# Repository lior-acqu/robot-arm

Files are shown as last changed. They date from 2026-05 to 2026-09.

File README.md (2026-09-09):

Welcome to Dedekind's GitHub repo. Here you can find:
- All the 3D files I used to print the robot.
- Three example C++ scripts to control the Arduino. More info on them below.
	- Rock-paper-scissors
	- Pick-and-place (called inversekinematics)
	- Manual servo control (servos)
# Scripts
## Rock-Paper-Scissors
When you run this script, you can play rock-paper-scissors with your robot arm. Opening the gripper means paper, closing it means rock, a quick open-close motion means scissors. Have fun!
## Pick-And-Place (inversekinematics)
In this script, you can make the robot pick up things like pens and erasers. If you use the same servos as I do, the weight of these objects is no problem.
The file contains many comments. If you need to change something in the script, you can find everything with ease. Possible things you may want to change:
- Positions: In the `loop()` function, you can change the numbers in the `inverseKin()` calls. The first number is the distance in cm from the shoulder joint. The second one is the angle of the base motor in degrees.
- Corrections: In case you have not been very precise in the assembly of the robot, and now, e.g. the shoulder joint is off by 10 degrees, you can enter corrections in the script that get taken into account by the inverse kinematics function. Just change `shoulder_corr` to `10`.
## Manual Servo Control (servos)
Here, you first run the Arduino script in the IDE. The robot will go to its home position.
Then, you open the `control.py` script. Here, you will probably need to change the `SERIAL_PORT` variable. You can find the right name for the port in the Arduino IDE in the top-left dropdown menu where you can select your Arduino board. Once the name is correct, you can run the script and then control all 5 servos with your keyboard.
- The base uses Q & A.
- The shoulder uses W & S.
- The elbow uses E & D.
- The wrist uses R & F.
- The gripper uses T & G.
# Known Issues
The robot arm works well. The points below are just small improvements.
1. Sometimes, the gripping motion does not work well. When it grabs a thin pen, the two gear racks sometimes lose contact with their rails and the gripper gear. The pen then drops on the ground and the two gear racks are now a bit wider apart.
	- Possible fix: The clamps should not be at the very end of the gear rack. Instead, they should have a safe margin of 1-2cm to make sure the gear rack is still fully supported by the guardrails.
2. Some parts are not designed in a way that they could be screwed in very tightly. They tend to be a bit loose.
	- Possible fix: Change the parts so that they are a bit easier to assemble, make things a bit tighter where you can.
# Materials
## 3D Parts
The uploaded parts work well. I usually added -0.07mm of X-Y-contour-compensation to make sure that the parts fit.
Support is not needed, except for `ForearmBase.stl` and `UpperArmBase.stl`.
My personal recommendation: Take my files only as an inspiration and design your own parts!
### Used Filament
I used eSUN's PLA+. I think that any regular filament (PLA, PETG) works just fine.
## Used Electronics
### Servos
- 2x MG996R (by Miuzei)
- 2x MG90S (by Miuzei)
- 1x SG90
### Other Electronics
- 10A 5V power supply (by Leicke, yes, it needs that much current)
- Arduino UNO
- PWM Servo Driver PCA9685
## Screws
- All screws are M3 (6mm & 10mm length) with matching nuts.
# Assembly
The assembly is quite intuitive, because there is always only one part that fits into the other part. Only a few remarks are necessary.
- The only place where you need 6mm M3 screws is when connecting the wrist motor to the gripper. In all other cases, 10mm is usually easier.
- The electronic parts do not need to be screwed into the base. The inner walls are designed to ensure perfect fit for all parts.
- In the base, there are some parts that are separated from the main part. Feel free to add weights into these parts. You can cover them with the printed weight caps.
- Each motor needs an attachment piece. In the middle of this attachment piece, just use the screw that was delivered in the same package as the motor. The MG996R motors have a separate attachment piece (`MG996RAttachment.stl`). The other ones use `NormalMotorAttachment.stl`.
- If the cables are too short for some motors, just use extension cables. I also did that.
- The base and the gripper both have small pockets where you can insert the nuts to make it easier to screw everything together.
- Be careful that all cables are plugged in correctly. 
If you have some more questions, just send me a message on LinkedIn (https://www.linkedin.com/in/liorporath/).

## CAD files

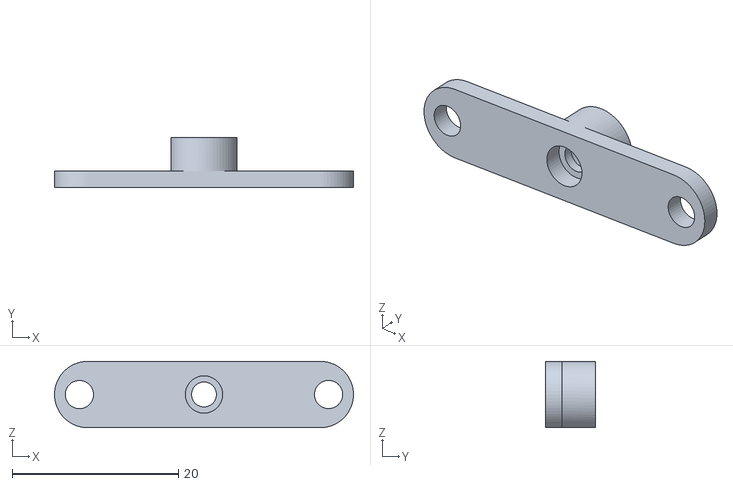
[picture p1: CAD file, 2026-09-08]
NormalMotorAttachment.stl
36.0 x 6.00 x 8.00

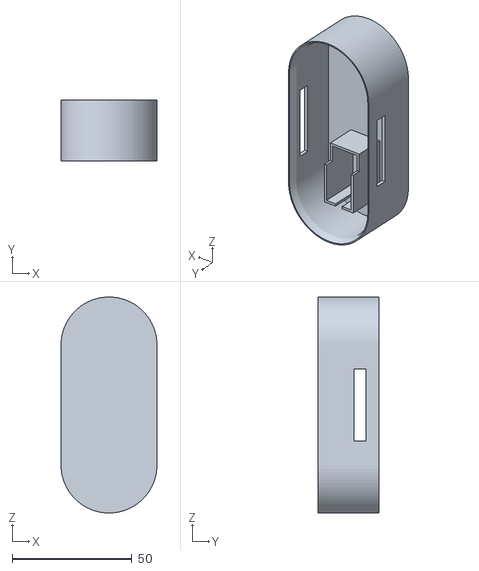
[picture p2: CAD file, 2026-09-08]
ForearmBase.stl
40.0 x 25.3 x 90.0

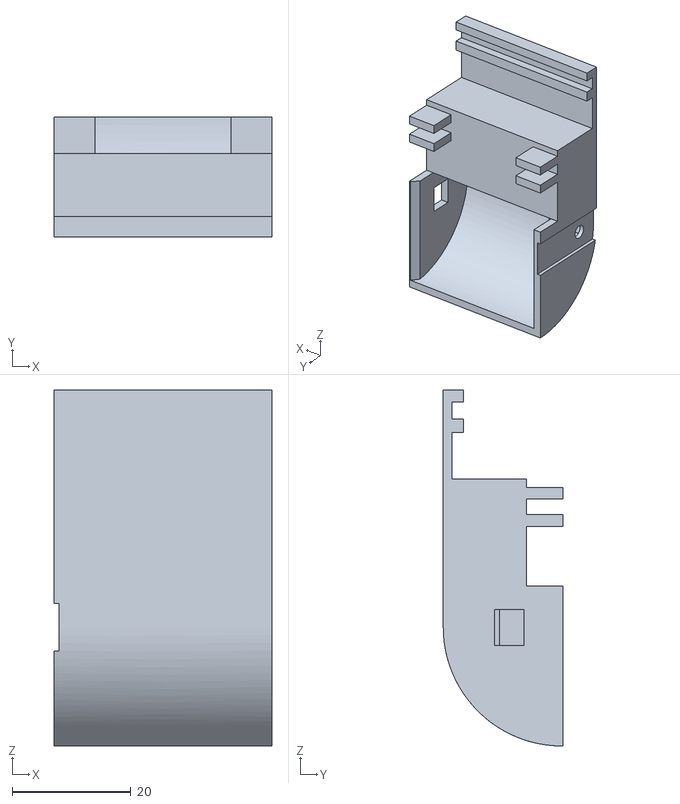
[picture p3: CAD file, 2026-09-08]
GripperCaseF.stl
36.7 x 20.1 x 60.0

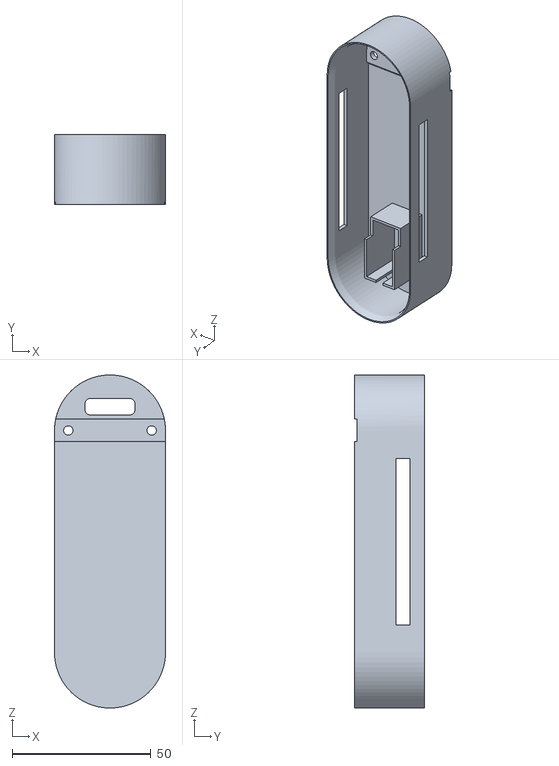
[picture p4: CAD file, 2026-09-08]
UpperArmBase.stl
40.0 x 25.3 x 120.0

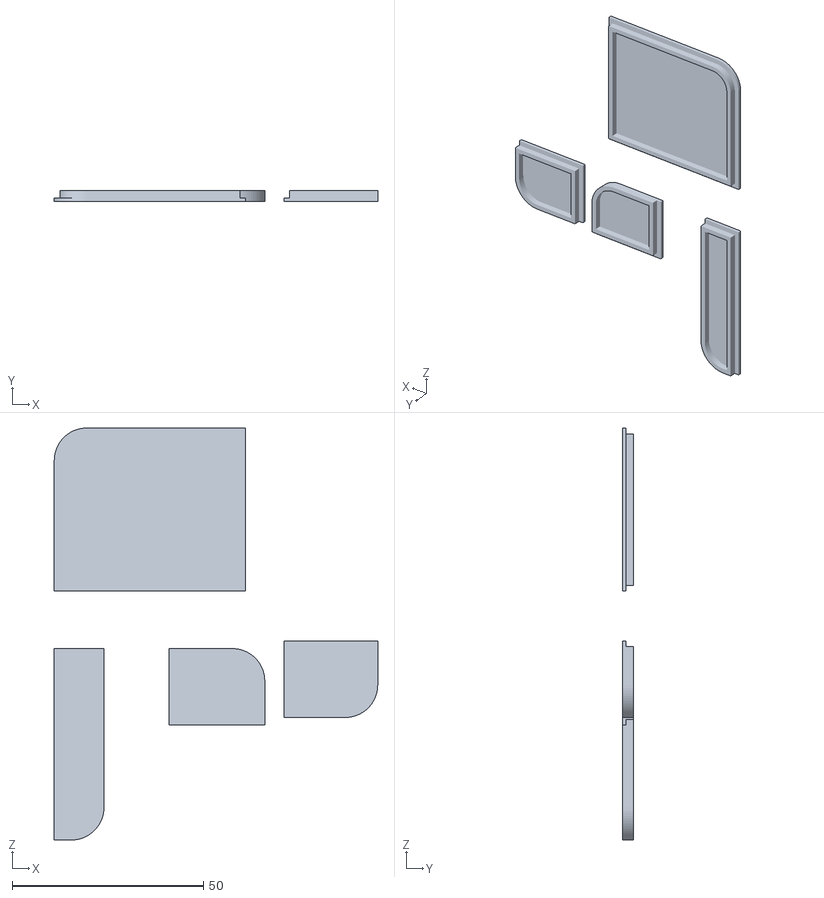
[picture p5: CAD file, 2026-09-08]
CapsForBaseWeights.stl
84.5 x 3.00 x 107.6

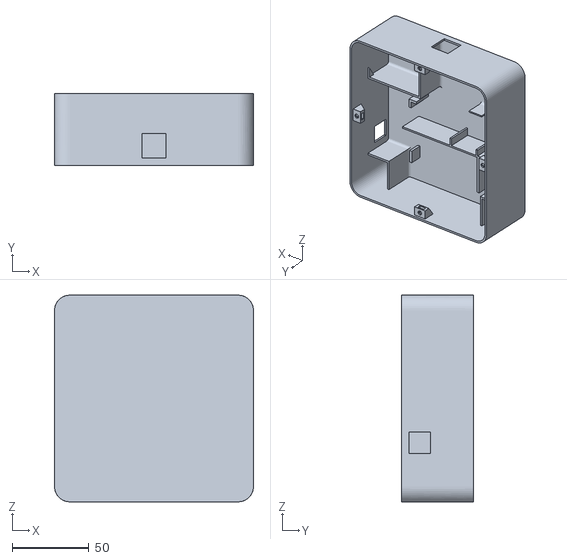
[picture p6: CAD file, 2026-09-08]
BaseBody.stl
130.0 x 47.0 x 135.0

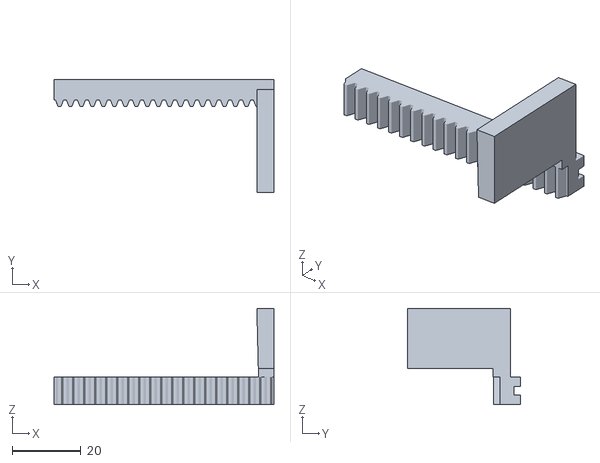
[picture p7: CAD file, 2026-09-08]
GearRack.stl
64.0 x 33.0 x 28.0

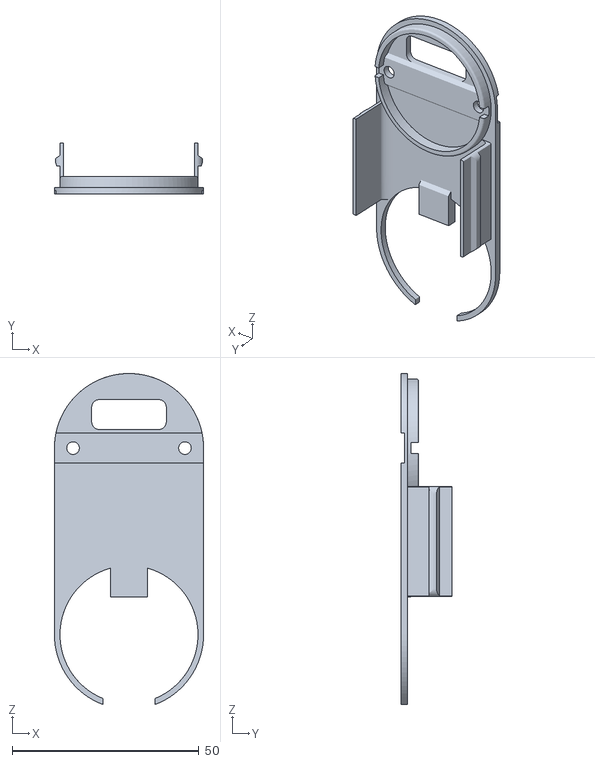
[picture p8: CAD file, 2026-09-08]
ForearmCap.stl
40.0 x 13.8 x 88.7

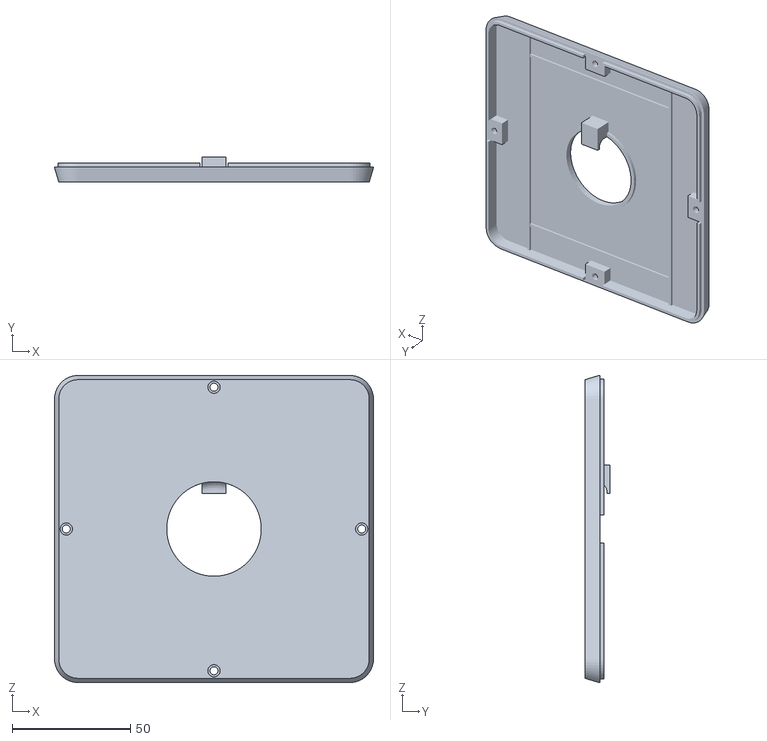
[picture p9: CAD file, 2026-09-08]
BaseCap.stl
135.0 x 10.6 x 130.0

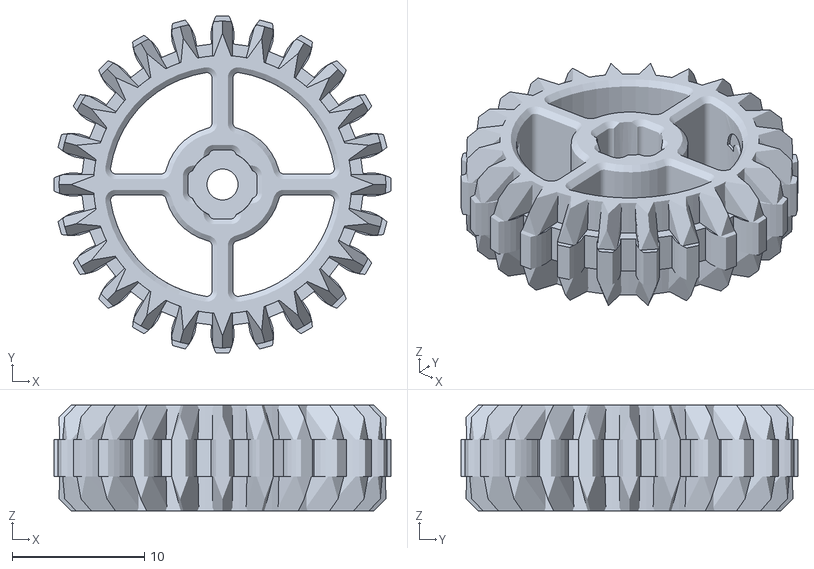
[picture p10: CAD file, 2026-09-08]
GripperGear.stl
25.5 x 25.5 x 8.00

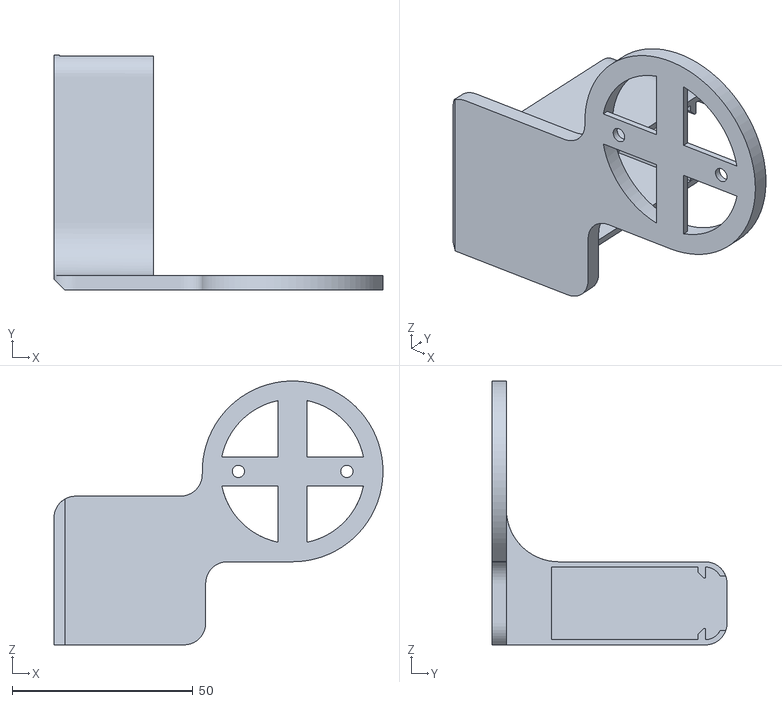
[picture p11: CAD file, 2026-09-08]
ConnectorBaseAndShoulder.stl
91.0 x 65.0 x 73.0

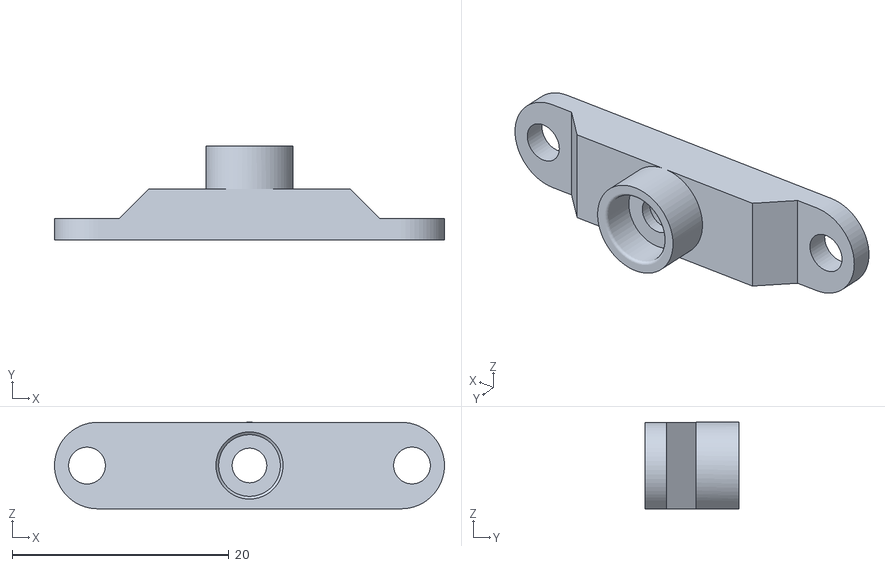
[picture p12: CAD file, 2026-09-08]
MG996RAttachment.stl
36.0 x 8.70 x 8.00

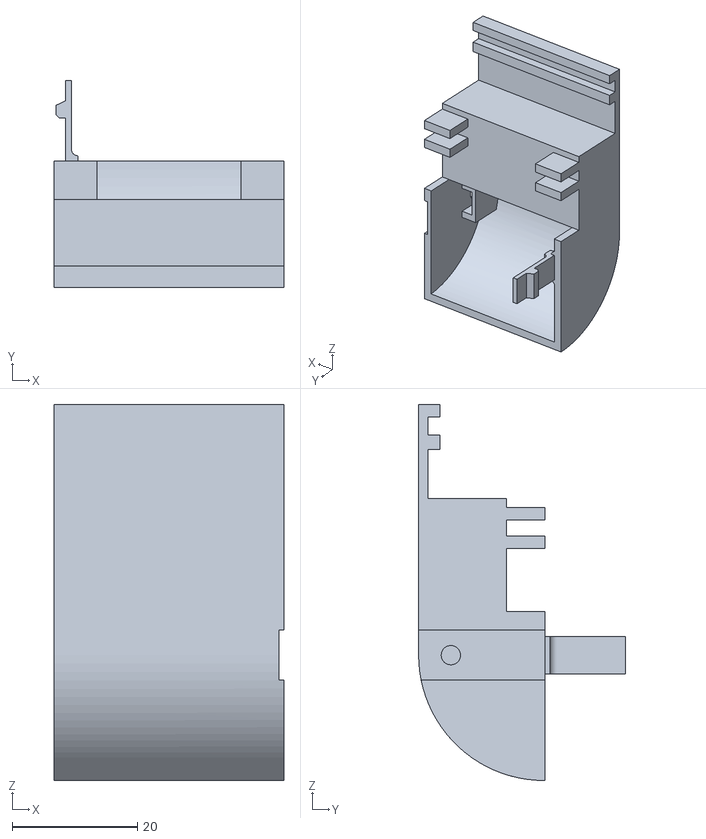
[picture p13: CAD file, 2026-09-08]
GripperCaseM.stl
36.7 x 33.0 x 60.0

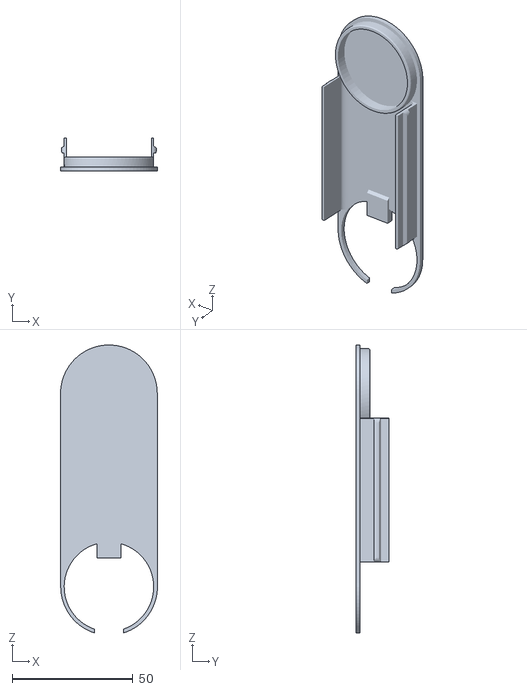
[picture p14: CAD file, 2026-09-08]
UpperArmCap.stl
40.1 x 13.8 x 119.1

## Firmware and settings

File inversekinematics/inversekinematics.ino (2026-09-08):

#include <Wire.h>
#include <Adafruit_PWMServoDriver.h>
#include <math.h>

Adafruit_PWMServoDriver pwm = Adafruit_PWMServoDriver();
#define SERVO_FREQ 50 

struct ServoLimits {
  int minPulse;
  int maxPulse;
};

ServoLimits config[] = {
  {150, 600}, // Motor 0: MG996R (Base)
  {150, 600}, // Motor 1: MG996R (Shoulder)
  {140, 580}, // Motor 2: MG90S  (Elbow)
  {140, 580}, // Motor 3: MG90S  (Wrist)
  {130, 550}  // Motor 4: SG90   (Gripper)
};

// Array to track the current angle of each motor (Starting at 90 degrees)
int currentAngles[] = {90, 90, 90, 90, 90}; 

// Change how intensely the motors move
int intensity = 4;

// measurements of arm
float l_under = 5;
float l_upper = 8;
float l_hand = 10;
float height = 10;

// Over time, the angles of the specific parts might slightly shift. To make sure that the inverse kinematics is still working, you can enter the approx. corrections of the angles below (in deg). 
// e.g. if shoulder_corr is 10, all calculated angles will be increased by 10 degrees.
float shoulder_corr = 0;
float elbow_corr = 0;
float wrist_corr = 0;

void inverseKin(int rad, int angle) {

  // move base according to angle
  int base[] = {0};
  moveMotorsSmooth(base, 1, angle, 1000);

  // how much difference there is between the wrist and the base in height
  float height_diff = l_hand - height;

  // calculating the distance betweeen wrist and shoulder to find the angle of the shoulder
  float dist = sqrt(rad*rad + height_diff*height_diff);

  //calculating elbow angle
  float elbow_value = (dist - l_upper)/l_under;
  float result_rad = asin(elbow_value); // Returns radians
  float elbow_deg = result_rad * 180.0 / 3.14159265; // Convert to degrees
  elbow_deg += (90 + elbow_corr);

  //setting elbow angle
  int elbow[] = {2};
  moveMotorsSmooth(elbow, 1, elbow_deg, 1000);

  //calculating shoulder angle
  result_rad = atan((l_under*sin(result_rad) + height_diff)/rad); // Returns radians
  float shoulder_deg = result_rad * 180.0 / 3.14159265; // Convert to degrees
  if (shoulder_deg < 0) shoulder_deg = 0;
  shoulder_deg += shoulder_corr;

  // calculating wrist angle
  float wrist_deg = elbow_deg - (90 - shoulder_deg);
  if (wrist_deg > 180) wrist_deg = 179;
  wrist_deg += wrist_corr;

   //setting wrist angle
  int wrist[] = {3};
  moveMotorsSmooth(wrist, 1, wrist_deg, 1000);

  //setting shoulder angle
  int shoulder[] = {1};
  moveMotorsSmooth(shoulder, 1, shoulder_deg, 1000);

}




// Moves multiple motors simultaneously from their current angles to their targets over duration in ms
void moveMotorsSmooth(int motorNums[], int numMotors, int targetAngle, int duration) {

  int startAngles[numMotors];
  for (int i = 0; i < numMotors; i++) {
    startAngles[i] = currentAngles[motorNums[i]];
  }

  const int stepDelay = 20; // ms per step
  int steps = duration / stepDelay;
  if (steps < 1) steps = 1;

  for (int step = 1; step <= steps; step++) {
    for (int i = 0; i < numMotors; i++) {
      int angle = startAngles[i] + (long)(targetAngle - startAngles[i]) * step / steps;
      moveMotor(motorNums[i], angle);
    }
    delay(stepDelay);
  }

  for (int i = 0; i < numMotors; i++) {
    currentAngles[motorNums[i]] = targetAngle;
  }
}




void setup() {
  Serial.begin(9600);
  pwm.begin();
  pwm.setPWMFreq(SERVO_FREQ);

  int m0[] = {0};
  moveMotorsSmooth(m0, 1, 90, 500);
  int m1[] = {1};
  moveMotorsSmooth(m1, 1, 90, 500);
  int m2[] = {2};
  moveMotorsSmooth(m2, 1, 90, 500);
  int m3[] = {3};
  moveMotorsSmooth(m3, 1, 90, 500);
  int m4[] = {4};
  moveMotorsSmooth(m4, 1, 90, 500);
}

void home() {
  int m1[] = {1};
  moveMotorsSmooth(m1, 1, 90, 1500);
  int m2[] = {2};
  moveMotorsSmooth(m2, 1, 90, 1000);
  int m3[] = {3};
  moveMotorsSmooth(m3, 1, 45, 1000);
  int m0[] = {0};
  moveMotorsSmooth(m0, 1, 90, 1500);
}


void grip() {
  int m4[] = {4};
  moveMotorsSmooth(m4, 1, 175, 500);
}

void release() {
  int m4[] = {4};
  moveMotorsSmooth(m4, 1, 30, 500);
}


void loop() { 
  // inverse kinematics of gripping motion
  // go to pos A
  inverseKin(10,45);
  delay(200);
  // grip object
  grip();
  delay(200);
  // lift it up
  home();
  delay(200);
  // put it down
  inverseKin(10,135);
  delay(200);
  // release it
  release();
  delay(200);
  // go home
  home();
  delay(200);
  // go to pos B
  inverseKin(10,135);
  delay(200);
  // grip object
  grip();
  delay(200);
  // lift it up
  home();
  delay(200);
  // put it down
  inverseKin(10,45);
  delay(200);
  // release it
  release();
  delay(200);
    // go home
  home();
  delay(200);
}


void moveMotor(int motorNum, int angle) {
  int pulse = map(angle, 0, 180, config[motorNum].minPulse, config[motorNum].maxPulse);
  pwm.setPWM(motorNum, 0, pulse);
}

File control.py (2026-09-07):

import serial
import time
from pynput import keyboard

# CHANGE THIS to match your Arduino's port (e.g., 'COM3' on Windows or '/dev/ttyACM0' on Mac/Linux)
SERIAL_PORT = '/dev/tty.usbmodem11101' 
BAUD_RATE = 9600

try:
    ser = serial.Serial(SERIAL_PORT, BAUD_RATE, timeout=1)
    time.sleep(2) # Wait for Arduino to reset
    print("Connected to Arduino! Use W/S (Shoulder), A/D (Base), Q/E (Elbow). Press ESC to quit.")
except Exception as e:
    print(f"Error connecting to serial port: {e}")
    exit()

def on_press(key):
    time.sleep(0.015) # prevent flooding with signals
    try:
        # Check which key was pressed and send a single character to Arduino
        if key.char == 'w': ser.write(b'W')
        elif key.char == 's': ser.write(b'S')
        elif key.char == 'a': ser.write(b'A')
        elif key.char == 'd': ser.write(b'D')
        elif key.char == 'q': ser.write(b'Q')
        elif key.char == 'e': ser.write(b'E')
        elif key.char == 'r': ser.write(b'R')
        elif key.char == 'f': ser.write(b'F')
        elif key.char == 't': ser.write(b'T')
        elif key.char == 'g': ser.write(b'G')
    except AttributeError:
        if key == keyboard.Key.esc:
            return False # Stop listener and quit

# Start listening to the keyboard
with keyboard.Listener(on_press=on_press) as listener:
    listener.join()

ser.close()

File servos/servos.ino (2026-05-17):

#include <Wire.h>
#include <Adafruit_PWMServoDriver.h>

Adafruit_PWMServoDriver pwm = Adafruit_PWMServoDriver();
#define SERVO_FREQ 50 

struct ServoLimits {
  int minPulse;
  int maxPulse;
};

ServoLimits config[] = {
  {150, 600}, // Motor 0: MG996R (Base)
  {150, 600}, // Motor 1: MG996R (Shoulder)
  {140, 580}, // Motor 2: MG90S  (Elbow)
  {140, 580}, // Motor 3: MG90S  (Wrist)
  {130, 550}  // Motor 4: SG90   (Gripper)
};

// Array to track the current angle of each motor (Starting at 90 degrees)
int currentAngles[] = {90, 90, 90, 90, 90}; 

// Change how intensely the motors move
int intensity = 4;

void setup() {
  Serial.begin(9600);
  pwm.begin();
  pwm.setPWMFreq(SERVO_FREQ);
  
  // Move all motors to initial home position (90 degrees)
  for(int i = 0; i < 5; i++) {
    moveMotor(i, currentAngles[i]);
    delay(1000);
  }
}

void loop() {
  if (Serial.available() > 0) {
    char incomingKey = Serial.read();
    
    switch (incomingKey) {
      // Base (Motor 0)
      case 'Q': currentAngles[0] += intensity; break;
      case 'A': currentAngles[0] -= intensity; break;
      
      // Shoulder (Motor 1)
      case 'W': currentAngles[1] += intensity; break;
      case 'S': currentAngles[1] -= intensity; break;
      
      // Elbow (Motor intensity)
      case 'E': currentAngles[2] += intensity; break;
      case 'D': currentAngles[2] -= intensity; break;

      // Wrist (Motor 3)
      case 'R': currentAngles[3] += intensity; break;
      case 'F': currentAngles[3] -= intensity; break;

      // Gripper (Motor 4)
      case 'T': currentAngles[4] += intensity; break;
      case 'G': currentAngles[4] -= intensity; break;
    }
    
    // Apply changes (limiting them between 0 and 180)
    for(int i = 0; i < 5; i++) {
      currentAngles[i] = constrain(currentAngles[i], 0, 180);
      moveMotor(i, currentAngles[i]);
    }
  }
}

void moveMotor(int motorNum, int angle) {
  int pulse = map(angle, 0, 180, config[motorNum].minPulse, config[motorNum].maxPulse);
  pwm.setPWM(motorNum, 0, pulse);
}
